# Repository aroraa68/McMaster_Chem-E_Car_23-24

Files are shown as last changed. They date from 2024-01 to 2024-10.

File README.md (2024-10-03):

# McMaster_Chem-E_Car_23-24
The codebase for the McMaster Chem-E Car Team from 2023-2024.

This project uses an Adafruit Feather RP2040 Adalogger microcontroller programmed in the Arduino programming language. The car runs off a chemical reaction and is stopped by a chemical reaction as well. However, the code and the microcontroller are used to start the stopping reaction and stir the mixture while monitoring it to identify when to stop based on a temperature threshold. It also uses an IMU to keep the car going straight, a servo for starting the stopping reaction, two motor drivers to run the drive motors, and a motor for stirring the stopping reaction. The car's main drive system will be powered from a custom-built Zn-Air battery while the remaining auxiliary systems are powered from a smaller Li-Po battery.

The major components used are as follows:<br />
2 - N20 100 RPM Motors (for drive system)<br />
1 - N20 1000 RPM Motor (for stirring mechanism)<br />
1 - SER0039 Servo Motor (for initially mixing reactants)<br />
2 - DRV8833 Motor Drivers<br />
1 - DS18B20 Temperature Sensor (for monitoring stopping reaction progress)<br />
1 - MPU-6050 IMU (for keeping the car going straight on the track)<br />
1 - Adafruit Feather RP2040 Adalogger Microcontroller<br />
1 - 1200 mAh Li-Po battery<br />

This repository also contains the custom-made PCB design for the component wiring we are using this year. The design was made using Altium, source files & gerber files are present in this repository.

The main objective of the competition is to design a small car to carry a certain amount of weight a set distance while powering and stopping the vehicle with a chemical reaction. The distance and weight vary each year. The compectition is hosted by the American Institute of Chemical Engineers (AIChE).

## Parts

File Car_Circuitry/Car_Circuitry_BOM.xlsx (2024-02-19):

Comment | Description | Designator | Footprint | LibRef | Quantity
2604-3102 | Connector | BAT_IN | 26043102 | 2604-3102 | 1
MP3213DH-LF-P | Integrated Circuit | BOOST1 | SOP65P490X110-9N | MP3213DH-LF-P | 1
TPS61023DRLT | Integrated Circuit | BOOST2 | SOTFL50P160X60-6N | TPS61023DRLT | 1
2.2 nF | Capacitor | C1, C12 | CAPC2012X75N | CL21B222KBANNNC | 2
10 nF | Capacitor | C2, C5, C6, C17 | CAPC2012X75N | CL21B103KBANNNC | 4
10 μF | Capacitor | C3, C7, C8, C14 | CAPC2012X140N | CL21B106KOQNNNE | 4
4.7 μF | Capacitor | C4 | CAPC2012X135N | CL21B475KOFNNNE | 1
2.2 μF | Capacitor | C9, C10 | CAPC2012X135N | CL21B225KAFNNWE | 2
100 nF | Capacitor | C11, C13 | CAPC2012X95N | CL21B104KBCNNNC | 2
22 μF | Capacitor | C15, C16 | CAPC3216X180N | CL31B226KPHNNNE | 2
SSA34HE3_A_I | Schottky Diode | D1 | DIONM5127X229N | SSA34HE3_A_I | 1
DRV8833PWPR | Integrated Circuit | DRV1, DRV2 | SOP65P640X120-17N | DRV8833PWP | 2
B3B-XH-A(LF)(SN) | CONN HEADER VERT 3POS 2.5MM | DS18B20_IN, SER0039_OUT | FP-B3B-XH-A_LF_SN-MFG | CMP-17439-000014-3 | 2
MPU6050 | IMU | IMU | MPU6050 | MPU6050 | 1
4.7 μH | Inductor | L1 | CDRH8D43NP4R7NC | CDRH8D43NP-4R7NC | 1
1 μH | Inductor | L2 | 74438357010 | 74438357010 | 1
B2B-XH-A(LF)(SN) | CONN HEADER VERT 2POS 2.5MM | M1_OUT, M2_OUT, M3_OUT, M4_OUT, SW_IN | FP-B2B-XH-A_LF_SN-MFG | CMP-2000-05888-3 | 5
Feather M0 Adalogger | Adafruit Microcontroller | MCU | 2796 | 2796 | 1
15 kΩ | Resistor | R1 | RESC3216X70N | RMCF1206FT15K0 | 1
10 kΩ | Resistor | R2 | RESC3216X70N | RMCF1206FT10K0 | 1
75 kΩ | Resistor | R3 | RESC3116X65N | RC1206FR-0775KL | 1
2.2 kΩ | Resistor | R4, R7 | RESAD1042W49L330D178 | RNMF14FTC2K20 | 2
180 mΩ | Resistor | R5, R8 | ERJ6_B_BW_R_LW_CW_D | ERJ-6DSFR18V | 2
330 mΩ | Resistor | R6, R9 | ERJ6_B_BW_R_LW_CW_D | ERJ-6DQFR33V | 2
4.7 kΩ | Resistor | R10 | RESAD1530W60L610D230 | CF1_4C472J | 1
100 kΩ | Resistor | R11 | ERJ8ENF1000V | ERJ-8ENF1003V | 1
732 kΩ | Resistor | R12 | ERJ8ENF1000V | ERJ-8ENF7323V | 1

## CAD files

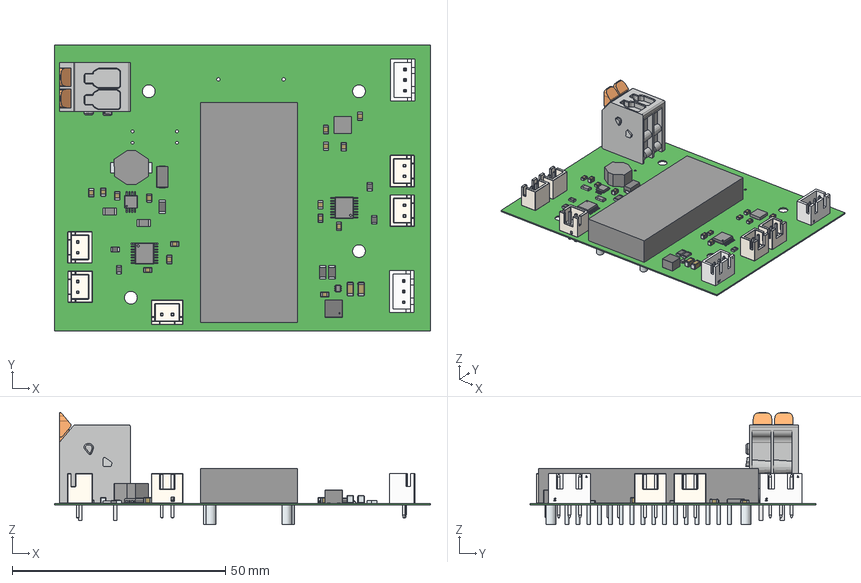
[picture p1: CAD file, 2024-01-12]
Car_Circuitry/Car_Circuitry.step
88.1 x 66.9 x 26.3 mm
FilletPin1
FilletPin2
body_SSMC_4030
land_pattern_SSMC_4020 x 2
Pins x 4
Marking x 2
JST Logo x 2
B2B-XH-A x 5
JST Logo adjustable x 5
solidBody x 6
Terminal x 6
solidTop x 6
R10
R7
R4
term1
term2
Leads x 32
PinsArrayLR x 3
ThermalPad x 3
BODY-SOT
PIN1-ID

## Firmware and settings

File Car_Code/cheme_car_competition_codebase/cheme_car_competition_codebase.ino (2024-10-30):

// TODO:
// Tune Kalman filtering for IMU & PID coefficients
// Add a comment
// Included libraries
#include <OneWire.h>
// #include <Wire.h>
// #include <MPU6050_light.h>
#include <DallasTemperature.h>
// #include <PID_v1_bc.h>
#include <Servo.h>
#include <Adafruit_NeoPixel.h>
#include "SdFat.h"

#define GND_PIN 4 // Tie pin 4 to GND for compatibility

#define NUM_PIXELS 1 // Status LED

// Define drive motor pins
#define right_pwm1 10
#define right_pwm2 9
#define left_pwm1 12
#define left_pwm2 11

// Define the PWM pins for the stir bar motor
#define stirPin1 24
#define stirPin2 A3

// Define the PWM pins for the linear actuator
#define linAcc1 6
#define linAcc2 5

// Define servo pin
#define servo_pwm 13

#define ONE_WIRE_BUS A1 // pin for the DS18B20 data line

// Define chip select pin for SD card
#define SD_CS_PIN 23

Servo servo; // Create servo object

// MPU6050 mpu(Wire); // Create MPU6050 instance

OneWire oneWire(ONE_WIRE_BUS);       // Create a OneWire instance to communicate with the sensor
DallasTemperature sensors(&oneWire); // Pass oneWire reference to Dallas Temperature sensor

Adafruit_NeoPixel pixel(NUM_PIXELS, PIN_NEOPIXEL, NEO_GRB + NEO_KHZ800); // Status LED

// Define files
SdFat SD;
File32 root;
File32 nextFile;
File32 dataFile;
SdSpiConfig config(SD_CS_PIN, DEDICATED_SPI, SD_SCK_MHZ(16), &SPI1);
String fileName;

bool isFileNew = true; // Checks for new file

// Time limit in milliseconds
// const unsigned long tLim = 120000;

// The target angle to keep car straight
// double goalAngle = 0.0;

// Define accelerometer variables
// double zAngle; // z-axis angle

// Temperature threshold
float tempDiff;

// Initialize run count for SD card file
int runCount;

// Temperature change
float tempChange;

// variables to store temperature
double temperatureC; // Current temperature
double initTemp;     // Initial temperature for differential calculation

double data[2]; // Data array

// KALMAN FILTER variables
double x_temp; // Filtered temperature
double p_temp; // Initial error covariance
// double x_MPU;  // Filtered temperature
// double p_MPU;  // Initial error covariance

// Process noise and measurement noise
double q_temp; // Process noise covariance
double r_temp; // Measurement noise covariance
// double q_MPU;  // Process noise covariance
// double r_MPU;  // Measurement noise covariance

// Keeping track of time
float currTime = 0;
unsigned long startTime;
bool firstRun = true;

// PID Loop variables
// double pidOutput; // The output correction from the PID algorithm

// The following numbers need to be adjusted through testing
// double Kp = 1; // Proportional weighting
// double Ki = 0; // Integral weighting
// double Kd = 0; // Derivative weighting

// Offset speeds for left and right wheel
// int left_offset = 0;
// int right_offset = 0;

// PID control object; input, output, and goal angle are passed by pointer.
// PID carPID(&x_MPU, &pidOutput, &goalAngle, Kp, Ki, Kd, DIRECT);

void drive_forward(int speed) // Drive function
{
  // Right wheel
  digitalWrite(right_pwm2, HIGH);
  analogWrite(right_pwm1, speed);
  // analogWrite(right_pwm1, speed - right_offset);

  // Left wheel
  digitalWrite(left_pwm2, HIGH);
  analogWrite(left_pwm1, speed + 9); // speed + 9 offset, to go straighter.
  // analogWrite(left_pwm1, speed - left_offset);
}

void stop_driving() // Stop function
{
  // Right wheel
  digitalWrite(right_pwm2, HIGH);
  analogWrite(right_pwm1, 255);

  // Left wheel
  digitalWrite(left_pwm2, HIGH);
  analogWrite(left_pwm1, 255);
}

void servo_dump() // Dump contents of bowl into braking vessel with servo
{
  servo.writeMicroseconds(2600); // Rotate to 180 deg position without delay
  delay(1000);                   // Wait 1 s
  servo.writeMicroseconds(500);  // Return to default position
}

void start_stir() // Start stirring mechanism
{
  analogWrite(stirPin1, 255);  // 100% to overcome stall
  digitalWrite(stirPin2, LOW); // For fast decay
  delay(1000);                 // Wait 1 s to spin up
  analogWrite(stirPin1, 146);  // 57% speed as per testing
}

void inject() // Inject syringe to initiate hydrogen reaction 
{
  analogWrite(linAcc1, 0);     // 100% power
  digitalWrite(linAcc2, HIGH); // For slow decay
  delay(25000);                // Wait to finish extending
  analogWrite(linAcc1, 255);   // Stop extending
}

// void PID_loop() // Update motor speeds according to PID algorithm
// {
//   carPID.Compute(); // Run compute algorithm and updates pidOutput

//   if (pidOutput > 0)
//   {
//     left_offset = abs(round(pidOutput)); // If output needs to be adjusted in positive dir (to the right), increase left wheel speed
//     right_offset = 0;                    // Zero other wheel offset to prevent instability
//   }
//   else if (pidOutput < 0)
//   {
//     right_offset = abs(round(pidOutput)); // If output needs to be adjusted in negative dir (to the left), increase right wheel speed
//     left_offset = 0;                      // Zero other wheel offset to prevent instability
//   }
//   else
//   {
//     left_offset = 0;
//     right_offset = 0;
//   }
// }

void kalman_filter(double x_k, double p_k, double q, double r, double input, bool tempTrue) // Kalman filtering algorithm
{
  // Kalman filter prediction
  double x_k_minus = x_k;     // Predicted next state estimate
  double p_k_minus = p_k + q; // Predicted error covariance for the next state

  // Kalman filter update

  /* Kalman gain: calculated based on the predicted error covariance
  and the measurement noise covariance, used to update the
  state estimate (x_k) and error covariance (p_k) */
  double k = p_k_minus / (p_k_minus + r); // Kalman gain

  // Comparison with actual sensor reading
  x_k = x_k_minus + k * (input - x_k_minus); // Updated state estimate
  p_k = (1 - k) * p_k_minus;                 // Updated error covariance

  if (tempTrue) // Update state for temperature sensor or IMU accordingly
  {
    x_temp = x_k;
    p_temp = p_k;
  }
  else
  {
    // x_MPU = x_k;
    // p_MPU = p_k;
  }
}

void printer(bool serialTrue, unsigned long millisTime, double outputs[2]) // Output function
{
  if (serialTrue) // Print data to serial or SD card file accordingly in .csv format
  {
    Serial.print(millisTime);

    for (int i = 0; i < 2; i++)
    {
      Serial.print(",");
      Serial.print(outputs[i]);
    }

    Serial.println("");
  }
  else
  {
    dataFile.print(millisTime);

    for (int i = 0; i < 2; i++)
    {
      dataFile.print(",");
      dataFile.print(outputs[i]);
    }

    dataFile.println("");
  }
}

void setup() // Setup (executes once)
{
  // Tie pin 4 to GND for compatibility
  pinMode(GND_PIN, OUTPUT);
  digitalWrite(GND_PIN, LOW);

  // Indicate status to be initialized
  pixel.begin();
  pixel.setBrightness(255);
  pixel.show();
  pixel.setPixelColor(0, 255, 0, 0);
  pixel.show();

  // Get time at start
  startTime = millis();

  while (!SD.begin(config)) {
    delay(1000); // Wait for a second before retrying
  }

  root = SD.open("/", FILE_READ); // Open SD root directory
  runCount = 0;

  while (true)
  {
    nextFile = root.openNextFile();

    if (nextFile)
    {
      runCount++; // Increment with each existing file
    }
    else
    {
      nextFile.close();
      break;
    }
  }

  root.close();

  // Setting to drive motors output mode
  pinMode(right_pwm1, OUTPUT);
  pinMode(right_pwm2, OUTPUT);
  pinMode(left_pwm1, OUTPUT);
  pinMode(left_pwm2, OUTPUT);

  stop_driving(); // Stop driving motors from residual bootloader code

  // Initialize the stir motor pins as outputs
  pinMode(stirPin1, OUTPUT);
  pinMode(stirPin2, OUTPUT);

  // Initialize the stir motor pins as outputs
  pinMode(linAcc1, OUTPUT);
  pinMode(linAcc2, OUTPUT);

  // Setting the stir speed
  start_stir();

  // Inject the contents of the syringe
  inject();
  
  sensors.begin();                       // Initialize the DS18B20 sensor
  sensors.requestTemperatures();         // Request temperature from all devices on the bus
  initTemp = sensors.getTempCByIndex(0); // Get temperature in Celsius

  // Wire.begin();             // Initialize I2C communication
  // mpu.begin();              // Initialize MPU6050
  // mpu.calcOffsets();        // Zero yaw angle
  // mpu.update();             // Update MPU readings
  // zAngle = mpu.getAngleZ(); // Get z-axis angle from MPU

  // Initialize Kalman filter parameters
  x_temp = initTemp; // Initial state estimate
  p_temp = 0.1;      // Initial error covariance
  q_temp = 0.01;     // Process noise covariance
  r_temp = 0.5;      // Measurement noise covariance
  // x_MPU = zAngle;    // Initial state estimate
  // p_MPU = 1.0;       // Initial error covariance
  // q_MPU = 0.01;      // Process noise covariance
  // r_MPU = 0.1;       // Measurement noise covariance

  // Initialize servo to default position
  servo.attach(servo_pwm, 500, 2600);
  
  // Dump reactants before starting drive
  servo_dump();

  // Activate PID
  // carPID.SetMode(AUTOMATIC);

  // The pid outputs between -51 to 51 depending on how the motors should be adjusted. An output of 0 means no change. (This should be adjusted through testing).
  // carPID.SetOutputLimits(-51, 51);

  pixel.setPixelColor(0, 0, 0, 255); // Indicate setup complete status
  pixel.show();

  // Start drive motors at full power to overcome stall
  drive_forward(0);
}

void loop() // Loop (main loop)
{
  sensors.requestTemperatures();             // Request temperature from all devices on the bus
  temperatureC = sensors.getTempCByIndex(0); // Get temperature in Celsius

  // mpu.update();             // Update MPU readings
  // zAngle = mpu.getAngleZ(); // Get z-axis angle from MPU

  // Update kalman filters
  kalman_filter(x_temp, p_temp, q_temp, r_temp, temperatureC, true);
  // kalman_filter(x_MPU, p_MPU, q_MPU, r_MPU, zAngle, false);

  // Get time on each measurement of sensor
  if (firstRun)
  {
    startTime = millis(); // First measurement saved seperately
    currTime = 0;         // Set current time to zero from start time
    firstRun = false;
  }
  else
  {
    currTime = (millis() - startTime)/1000; // Taken to check time against first measurement
  }

  // Open csv file
  fileName = "Run_" + String(runCount) + ".csv";
  dataFile = SD.open(fileName, FILE_WRITE);

  if (dataFile)
  {
    // Writes header if it's a new file
    if (isFileNew)
    {
      dataFile.println("Time,Temperature,Filtered Temperature");
      isFileNew = false;
    }

    // Update data array
    data[0] = temperatureC;
    data[1] = x_temp;

    // Write variable data to the file in CSV format
    printer(false, currTime, data);

    dataFile.close();
  }

  tempDiff = -0.068*currTime + 1.4; // Update temperature differential
  tempChange = x_temp - initTemp; // Calculate temperature change

  drive_forward(128); // 50% speed in slow decay mode

  // // Update PID model
  // PID_loop();

  // if (tempChange >= tempDiff)
  // {
  //   // Stop driving
  //   stop_driving();

  //   // Indicate status to be finished
  //   pixel.setPixelColor(0, 0, 0, 255);
  //   pixel.show();

  //   while (1)
  //     ; // Do nothing for remainder of uptime
  // }
}

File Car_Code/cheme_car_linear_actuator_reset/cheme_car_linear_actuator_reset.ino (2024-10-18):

#include <Adafruit_NeoPixel.h>

// Define the PWM pins for the linear actuator
#define linAcc1 6
#define linAcc2 5

#define NUM_PIXELS 1 // Status LED

Adafruit_NeoPixel pixel(NUM_PIXELS, PIN_NEOPIXEL, NEO_GRB + NEO_KHZ800); // Status LED

void retract() // Retract actuator to reset hydrogen reaction 
{
  analogWrite(linAcc2, 0);     // 100% power
  digitalWrite(linAcc1, HIGH); // For slow decay
  delay(15000);                // Wait to finish extending
  analogWrite(linAcc2, 255);   // Stop extending
}

void setup() // Setup (executes once)
{
  // Initialize the stir motor pins as outputs
  pinMode(linAcc1, OUTPUT);
  pinMode(linAcc2, OUTPUT);
  
  // Indicate status to be initialized
  pixel.begin();
  pixel.setBrightness(255);
  pixel.show();
  pixel.setPixelColor(0, 255, 0, 0);
  pixel.show();
   
  retract(); // Extend syringe to reset
  
  // Indicate status to be finished
  pixel.setPixelColor(0, 0, 0, 255);
  pixel.show();
}

void loop() // Loop (main loop)
{
	// Do nothing
}

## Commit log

2023-11-11 initial code and PCB design
    [Car_Circuitry.PcbDoc, Car_Circuitry.PrjPcb, Car_Circuitry.SchDoc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]
2023-11-12 Updated trace routing.
    [Car_Circuitry.PcbDoc, Car_Circuitry.PrjPcb, Car_Circuitry.SchDoc]
2023-11-12 updated schematic component designations.
    [Car_Circuitry.PcbDoc, Car_Circuitry.PrjPcb, Car_Circuitry.SchDoc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]
2023-11-13 Changed inductors & boost converter layouts.
    [Car_Circuitry.PcbDoc, Car_Circuitry.SchDoc, Car_Circuitry.step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]
2023-11-13 untented vias in pcb.
    [Car_Circuitry.PcbDoc]
2023-11-14 Final changes to PCB.
    [Car_Circuitry.PcbDoc, Car_Circuitry.SchDoc, Car_Circuitry.step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]
2023-11-18 Update temp sensor code
2023-11-30 Updated pin assignments & diode part # (backorder)
    [Car_Circuitry.PcbDoc, Car_Circuitry.PrjPcb, Car_Circuitry.SchDoc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]
2024-01-01 Minor changes to pinout based on physical board.
    [Car_Circuitry.PcbDoc, Car_Circuitry.SchDoc, Car_Circuitry.step]
2024-01-12 Replaced backordered part with equivalent.
    [Car_Circuitry.PcbDoc, Car_Circuitry.PrjPcb, Car_Circuitry.SchDoc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]
2024-01-14 Updated pin assignment from 23 to A1
2024-01-15 initial code for stir bar motor
    speed is set to 80% and PWM pins are 5 and 6
2024-01-15 initial code for stir bar motor
    same as with datalogging, pins 5 and 6 are set for PWM with constant speed set to 80%
2024-01-15 changed variable name from "motorPin" to "stirPin"
2024-01-23 update code to reflect logic for forward PWM and fast decay
2024-01-23 Update cheme_car_datalogging_codebase.inupdate code to reflect logic for forward PWM and fast decayo
2024-01-30 removed delay to prevent code halting & cleaned formatting.
    [cheme_car_competition_codebase.ino, cheme_car_datalogging_codebase.ino]
2024-01-30 added current time to serial output.
2024-01-30 updated formatting, added temp sensor code to competition codebase to speed things along, & added drive code to datalog to see drive effects.
2024-01-31 Added printer function to streamline csv output.
2024-02-06 PID functionality
2024-02-06 removed buffer, set PID to 1,0,0, and included PID_loop in main loop
2024-02-12 PID added & updated to fix compilation errors. Comments updated.
    [cheme_car_competition_codebase.ino, cheme_car_datalogging_codebase.ino]
2024-02-13 Made changes to reflect preliminary testing done for motors.
2024-02-13 Replaced stir motor pins temporarily due to testing board defect. & start motors at full torque to overcome stall.
    [cheme_car_competition_codebase.ino, cheme_car_datalogging_codebase.ino]
2024-02-13 Updated pin assignments so all motors are in right orientation.
2024-02-13 Made changes to PID to prevent overflow.
    [cheme_car_competition_codebase.ino, cheme_car_datalogging_codebase.ino]
2024-02-19 added assembly drawing to PCB
    [Car_Circuitry.PrjPcb, Car_Circuitry_BOM.xlsx]
2024-02-19 servo motor code
2024-02-19 Changed formatting, added servo commands to datalogging codebase.
2024-02-20 Added IMU code & updated status LED, formatting, & servo code. Made kalman filtering function.
2024-02-20 uncommmented PID loop
2024-02-21 Minor formatting changes & updates to PID to prevent uncontrolled speed increase in overshoot conditions.
    [cheme_car_competition_codebase.ino, cheme_car_datalogging_codebase.ino]
2024-03-06 Updated pins & kalman filter parameters
2024-06-16 Commented out portions that didn't make the cut for competition.
    [cheme_car_competition_codebase.ino, cheme_car_datalogging_codebase.ino, cheme_car_linear_actuator_reset.ino]
2024-10-03 Update code to work with RP2040 drop-in replacement MCU to solve bootloader issues, fixed compatibility & prepared for nationals competition.
    [cheme_car_competition_codebase.ino, cheme_car_datalogging_codebase.ino, cheme_car_linear_actuator_reset.ino]
